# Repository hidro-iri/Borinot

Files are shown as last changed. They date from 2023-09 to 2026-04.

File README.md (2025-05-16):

# Borinot 🐝

<p align="center">
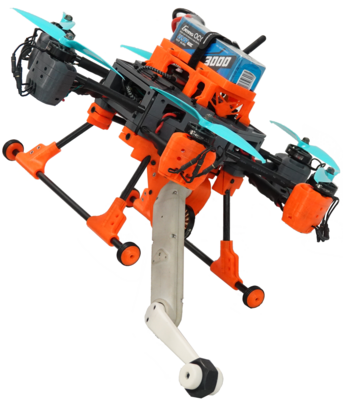
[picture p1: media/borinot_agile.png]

</p>

Borinot is an open-source, torque-controlled Unmanned Aerial Loco-Manipulator developed by the HiDRo group.  
It dynamically reconfigures its extremity as:
- A **tail** for agile flight  
- A **hand** for aerial manipulation  
- A **leg** for hybrid aerial-contact locomotion  

**Watch the demo**: [YouTube Presentation](https://www.youtube.com/watch?v=Ob7IIVB6P_A)

## Documentation  
Start by understanding the architecture and then assembling, configuring, and operating Borinot: 

| | |
| --- | --- |
| [**Borinot architecture**](architecture/README.md) | Understand the hardware and software architectures of Borinot |
| [**Hardware Assembly**](hardware/README.md) | Components list and instructions for assembling Borinot |
| [**Software Setup**](software/README.md) | Guide to Borinot's software stack installation, configuration, and subsystem integration |
| [**Operation Manual**](operation/README.md) | Instructions for operating Borinot and troubleshooting |

---

## Citation  
If Borinot contributes to your research, please cite:  

<!-- J. Martí-Saumell, H. Duarte, P. Grosch, J. Andrade-Cetto, A. Santamaria-Navarro, J. Solà. Borinot: an open thrust-torque-controlled robot for research on agile aerial-contact motion. arXiv preprint arXiv:2307.14686, 2023.-->

```bibtex
@misc{marti2023borinot,
  title={Borinot: An Open Thrust-Torque-Controlled Robot for Agile Aerial-Contact Motion Research},
  author={Martí-Saumell, Josep and Duarte, Hugo and Grosch, Patrick and Andrade-Cetto, Juan and Santamaria-Navarro, Angel and Solà, Joan},
  journal={arXiv preprint arXiv:2307.14686},
  year={2023}
}
```

## License
Borinot is licensed under the BSD 3-clause license. See [LICENSE](LICENSE) for details.

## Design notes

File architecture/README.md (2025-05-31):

# Borinot architecture

Borinot consists of hardware and software, both within the robot body and outside as necessary support elements.

This chapter describes the architecture. 

> You can click on the images below to get them in full resolution.

## Hardware

The Borinot robot consists of a flying platform and an arm, and is supported by some external equipments such as the Radio controller, the WIFI router, Optitrack and the base station or Laptop.

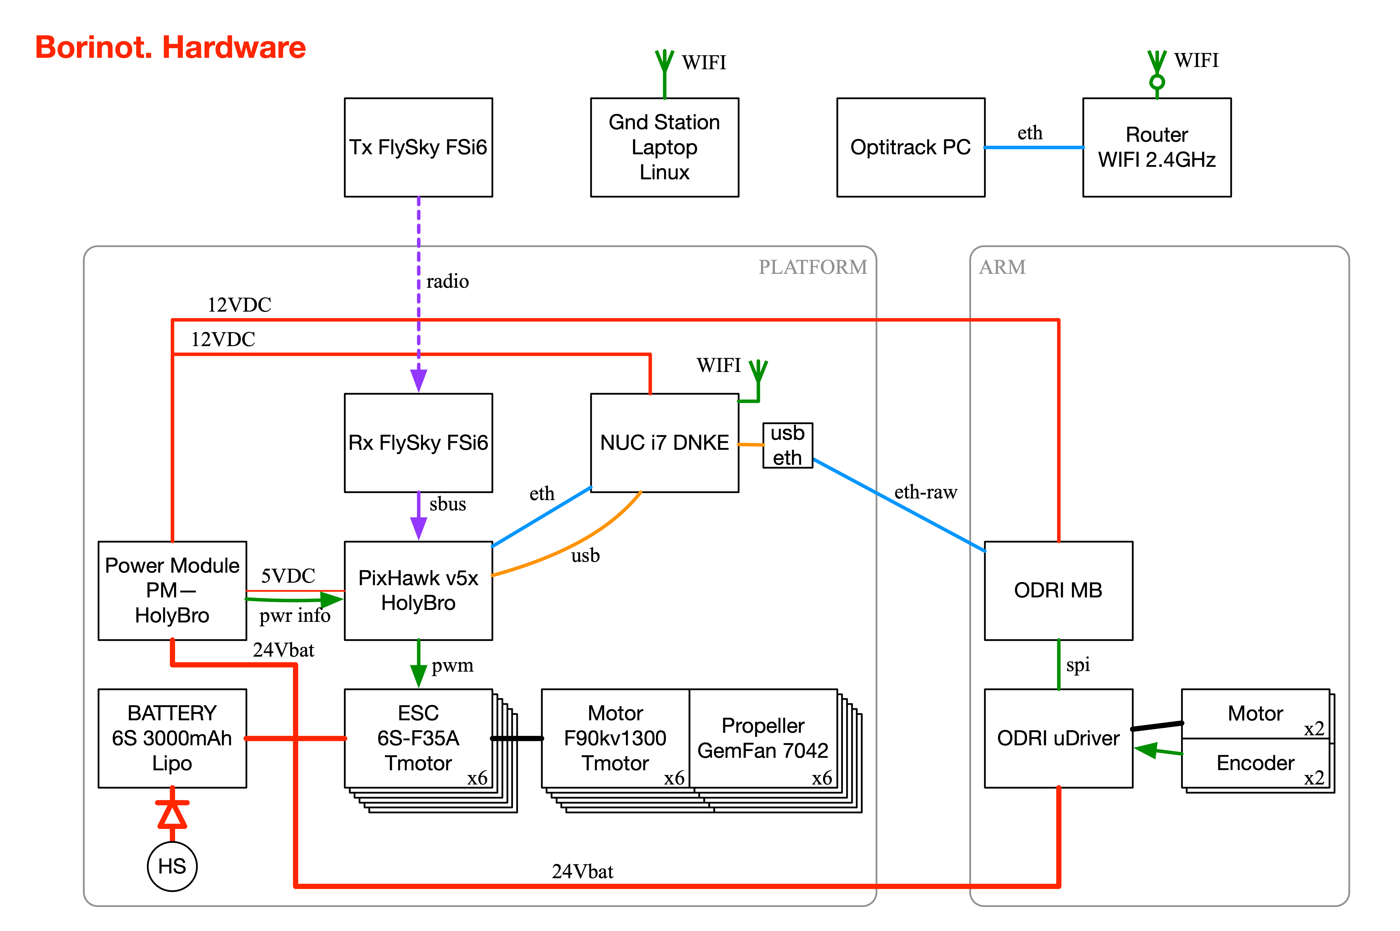
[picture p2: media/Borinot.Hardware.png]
Borinot Hardware


## Software

Borinot runs many pieces of software. Here, we detail the information flow for *estimation* (from sensors to computer) and *control* (from computer to motors). We also show the data flow for *simulations*.

### Software for state estimation

State estimation consists of fusing Borinot's IMU data with Optitrack position and orientation data.

The fusion is performed in the PixHawk unit by the EKF2 module.

The IMU data is gathered directly by PX4 in PixHawk

The Optitrack data is transferred from the Optitrack computer via wifi to Borinot's NUC, then via Ethernet to PX4 in Pixhawk.

The result of the estimation is send back to the NUC.

Additionally, the ODRI master board reports the arm state to the NUC via Ethernet.

The state `X` is located in the ROS2 node `StatePubSub`

Beware there are thre different reference frame conventions:
  - Optitrack uses `FUR`
  - PX4 uses `FRD`
  - ROS2 and Eagle MPC use `FLU`
  - The node `StatePubSub` in NUC transforms messages

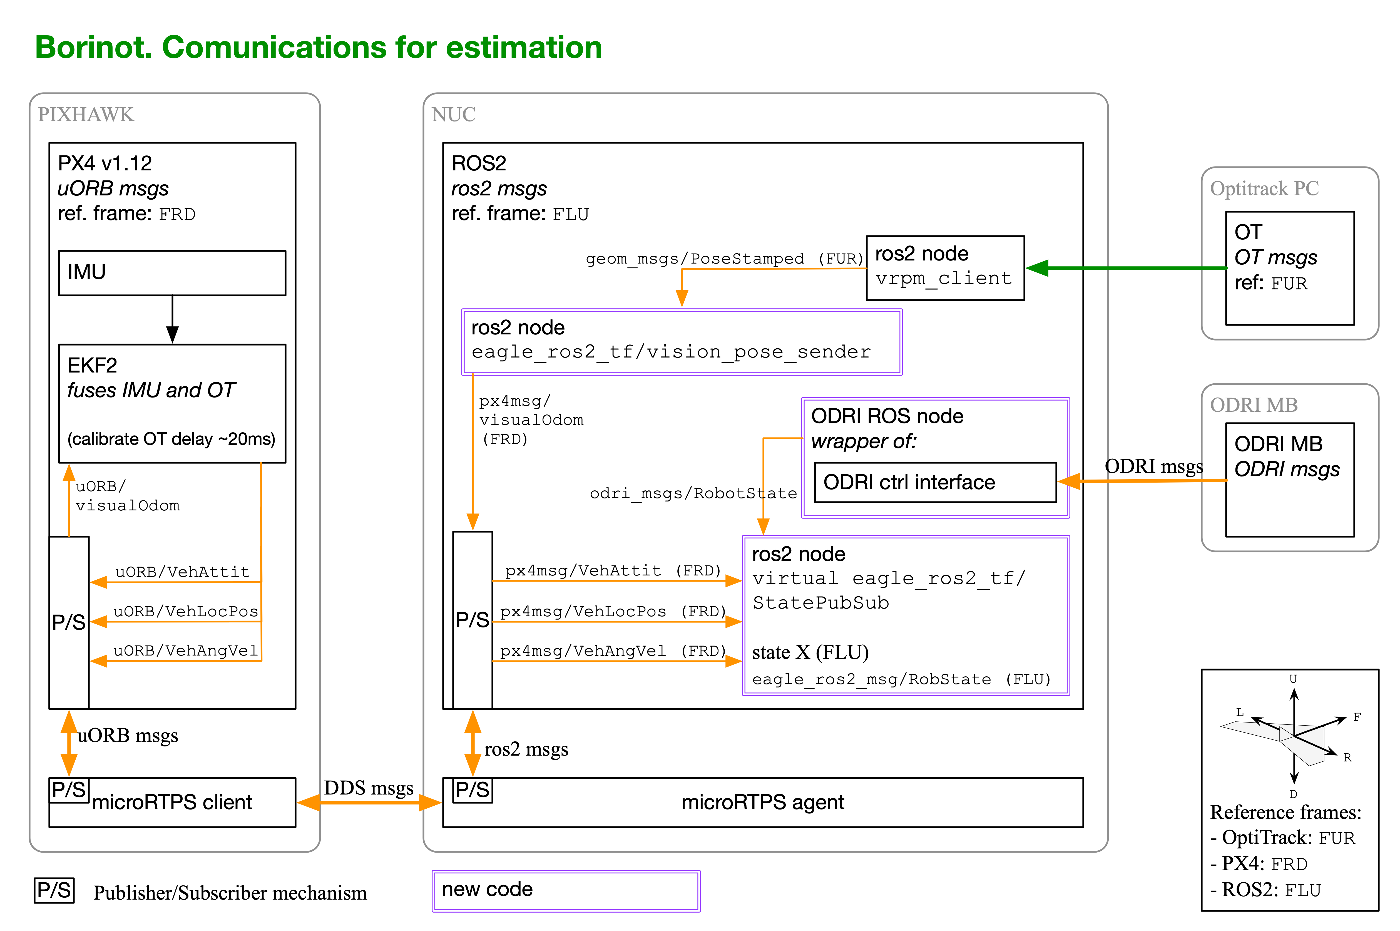
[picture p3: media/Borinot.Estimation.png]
Borinot Estimation


### Software for Control

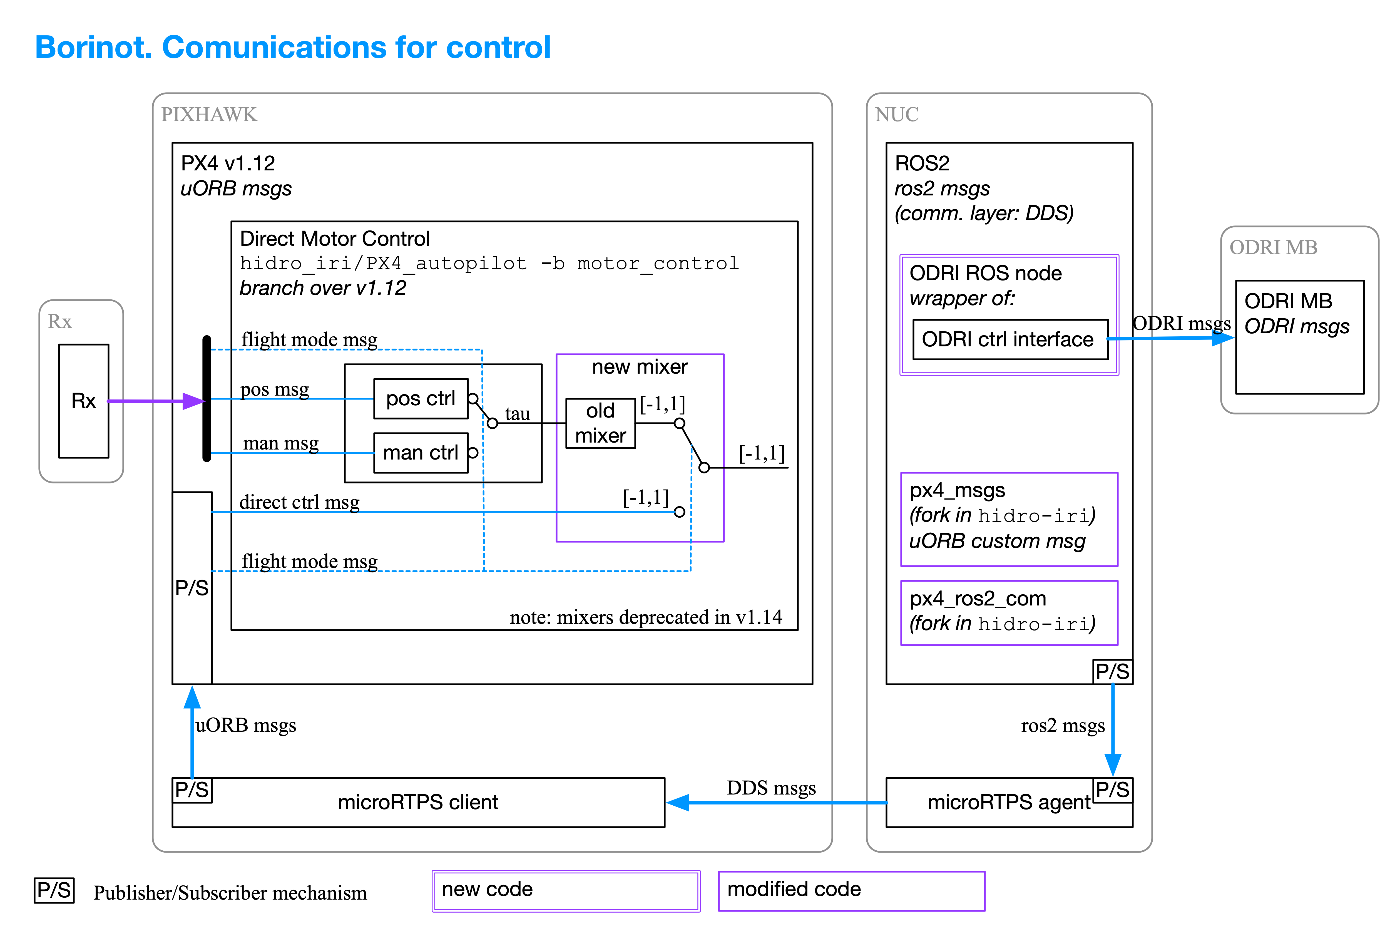
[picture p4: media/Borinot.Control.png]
Borinot Control


### Software for Simulation

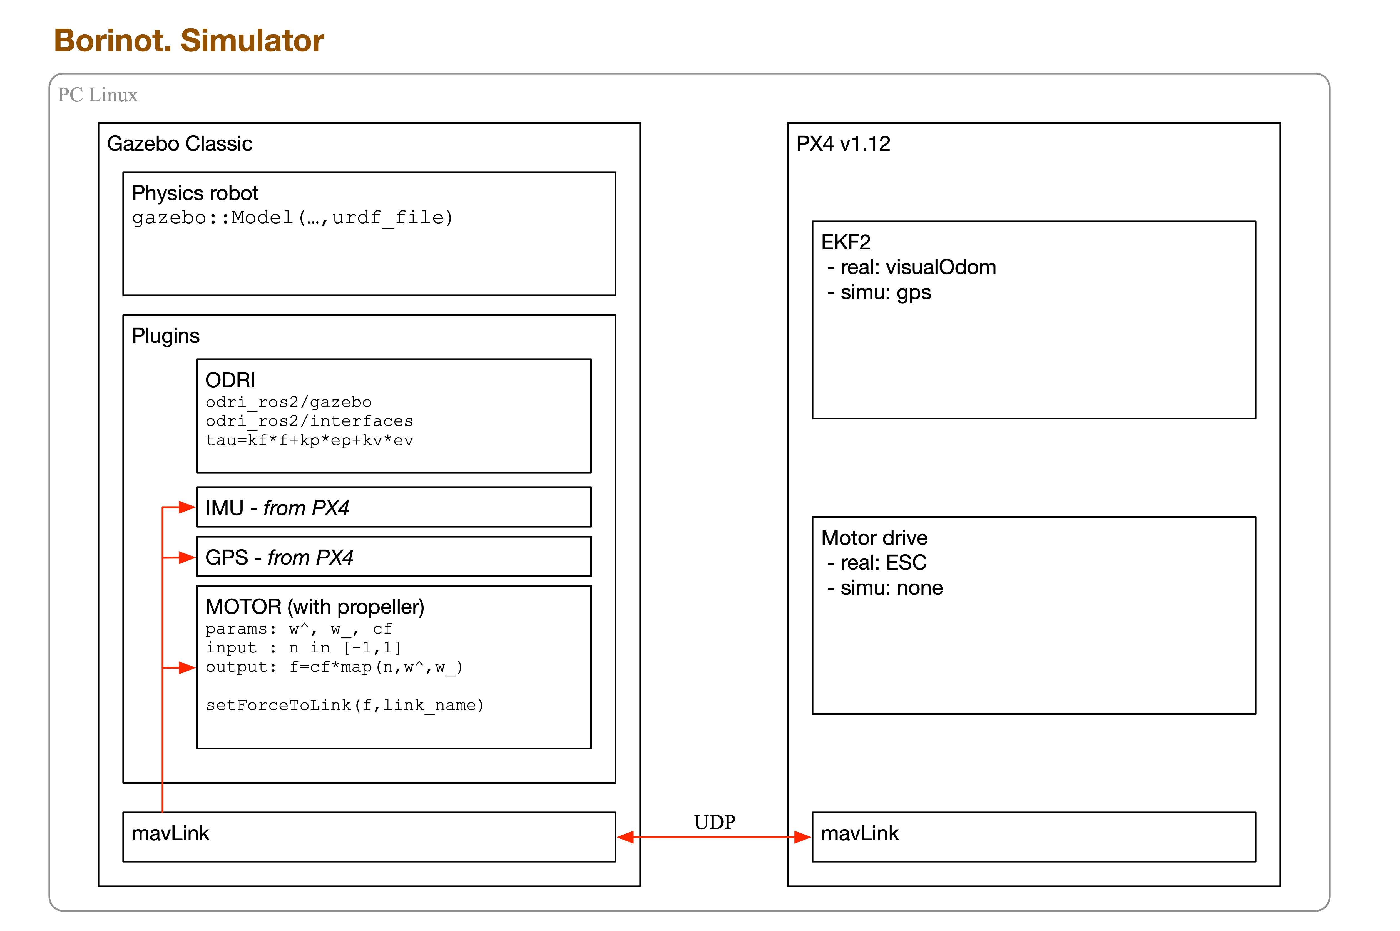
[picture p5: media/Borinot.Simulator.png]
Borinot Simulation


---

| [Top of page](#architecture) | [Back to Borinot HOME](../README.md) |
| --- | --- |

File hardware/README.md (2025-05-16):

# Borinot: Hardware Building Instructions

This guide provides a step-by-step overview of assembling Borinot. The assembly process is divided into two main sections: the **upper body** (steps 1 to 4) and the **lower body** (steps 5 to 7). Before you begin, ensure you have the necessary components (step 0).

**Contents:**

0. [**Components List**](0_components_list.md) - Full inventory of required parts.
1. [**Component Preparation**](1_component_preparation.md) - Modify power module and prepare motors/ESCs.
2. [**Airframe Assembly**](2_airframe_assembly.md) - Build motor cases and carbon fiber frame.
3. [**Main Body Assembly**](3_main_body_assembly.md) - Assemble core electronics in the main body case.
4. [**Upper Body Integration**](4_upper_body_integration.md) - Attach airframe to main body and route cables.
5. [**Landing Gear Assembly**](5_landing_gear_assembly.md) - Construct landing gear with dampers.
6. [**Flying Arm Assembly**](6_flying_arm_assembly.md) - Assemble ODRI actuator and controller case.
7. [**Lower Body Integration**](7_lower_body_integration.md) - Connect flying arm to landing gear and electronics.
8. [**Final Assembly**](8_final_assembly.md) - Combine upper and lower bodies.

---

| [Top of page](#borinot-hardware-building-instructions) | [Back to Borinot HOME](../README.md) |
| --- | --- |

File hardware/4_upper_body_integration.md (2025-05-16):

# Upper Body Integration

## 3D part 

### Materials

- 3d parts (spacers)
- nuts M3 (x8)

### Steps

1. clean plastic
2. put nuts

## Airframe Mounting

### Materials

- Main Body
- Airframe
- 3D parts

### steps

1. Place the main body on top of the airframe keeping the fronts align.
> :information_source: each CF tube should fit inside the CFT slots.  
> ⚠️  if one triangle does not fit, place properly two tubes and reassemble the two others motor cases to make the third bare fits.  
2. Put the medium spacer between the differents carbon fiber tubes and tight them with fasterner.
> ⚠️  The slots should be facing out.  
> :information_source: The spacer is place at the intersections of the carbon fibers tube. (seeing from the top)  
> :information_source: use the main body's inside cavity to hide the head of the fasteners.
> ⚠️  be careful to not fastern cables in it.
> :Cut the oer part of the fasterner. 

3. Put all the other spacers where they should go.
> ⚠️  The slots should be facing out.  
> :information_source: The spacer is place at the intersections of the carbon fibers tube. (seeing from the top)  
> :information_source: The more distance between two tubes, the bigger the spacers

4. For each landing gear interface, put it in place and tight it using fasterner.
> ⚠️  The slots should be facing out.  
> :info_source: The interface should fit just below the spacer.
> :information_source: use the main body's inside cavity to hide the head of the fasteners.
> ⚠️  be careful to not fastern cables in it.
> :Cut the oer part of the fasterner. 

- 2. Put one spacer between the differents carbon fiber tubes (start with the medium ones, then the big ones, then the small one).

- smaller between top and middle
- medium between middle and bottom
- large between top and bottom

- 3. if the spacer if touching the lower bares (small and big ones), put the associate landing gear interface below the spacer

- 4. Tight the airframe to the main body where the spacer is using fasteners

- 5. repeat steps 2 to 4 for each spacer.

## Upper Body Routing

> ⚠️  Patience is key.

### Materials

- USB-C cable
- receiver cable
- spiral attach

### steps

> Put a top view of the frame with the bar colored with the type of cable that should be passing through.

Motors connected to the Power module back : 1, 4, 6
Motors connected to the Power module front : 2, 3, 5

- signal cable goes to the bare that put them close to the back of the Pixhawk

1. Follow the routing schematic. (picture showing on which should pass each cable.)
    > Signal and Power cables should be twisted properly to ensure 
2. Continue with the signal cables.
3. Start by the power cables
4. Connect the signal cable following the [Hexarotor X airframe reference](https://docs.px4.io/main/en/airframes/airframe_reference.html#hexarotor-x). 
    > :information_source: To identify the proper cable (i.e cable number i) between all, proceed as follow: maintain the signal cable i on the motor side (as you are sure it is the good one), on the pixhawk side, pull each cable one by one, if you feel some force on the motor side, you have the good one!

4. Finish with the other cables.
    - From Pixhawk : ethernet !!! , power (should be already connected at main body assembly), serial bus (usb-c) [also to pixhawk] !!!,
    - From the computer : ethernet extender !!!, wifi antenna,
    - From power module : microcontroller cable, masterboard cable,
    - From radio receiver : two antennas,  radio receiver, 

5. Put the spiral to maintain the cable with the frame.
    - cable should pass below the tube
    - `Assure that the cables are properly twisted!!!`
    - Radio antenna should be put above the tube

6. 
---

| [Top of page](#upper-body-integration) | [Back to Hardware Building Instructions](README.md) | [Back to Borinot HOME](../README.md) | [Next → Landing Gear Assembly](5_landing_gear_assembly.md) |
| --- | --- | --- | --- |

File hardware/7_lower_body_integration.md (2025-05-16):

# Borinot: Lower Body Assembly Guide

The lower body is an important part of borinot. It's contains the arm and the associated low level controller and the landing gear. This part can be assembled to Borinot to give him access to an arm.

## Components List

| Part Name | Quantity | Description | Reference |
|---|:---:|---|---|
| [Controller Case - 3D Kit](CAD/platform/) | 1 | - | [Link to the part](CAD/platform/) |
| Master Board | 1 | - | - |
| Micro Driver | 1 | - | - |
| M2 Nuts | 4 | - | - |
| M2.5 Nuts | 4 | - | - |
| M2x6mm Screws | 4 | - | - |
| M2.5x6mm Screws | 4 | - | - |

## Assembly Guide

### Prerequisite: Landing Gear and Flying Arm

The [Landing Gear](landing_gear.md) and the [Flying Arm](flying_arm.md) have they own guide to simplifly the assembly. Please go refer to them if these parts are not yet assembled.

### Part 1: Controller Case

The controller case contains all the electronics require to control the arm. It contains a microcontroller have is connected to the motors and encoders of the arm. It also contain the masterboard, interface between the computer and the microcontroller. Both of these board are powered using the Power module contains in the Upper Body. In order to assemble it properly, we have to first clean the 3D printing and put the nuts and other mechanical components together. After that the boards have to be connected together and finally we can assemble everything.

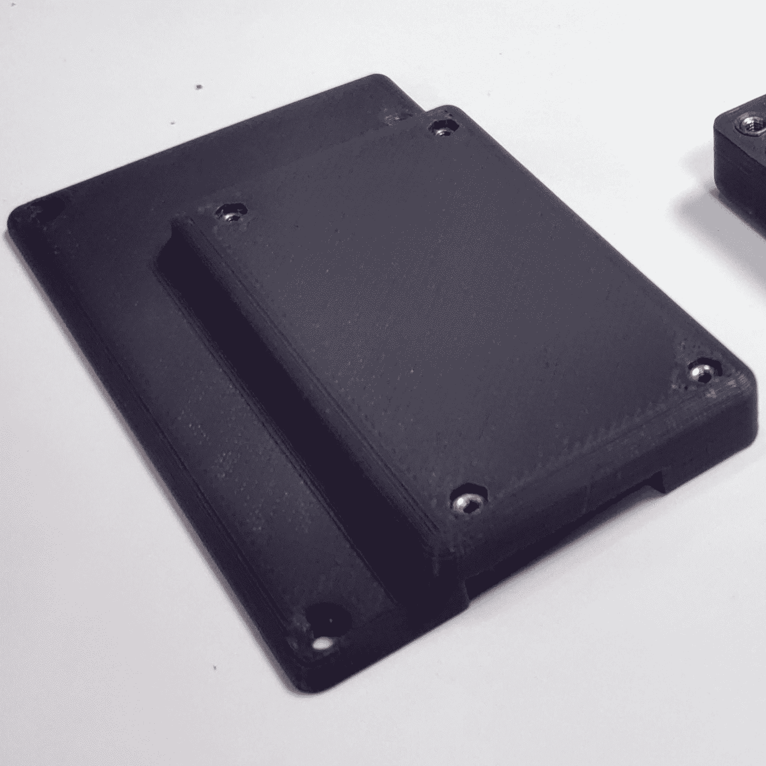
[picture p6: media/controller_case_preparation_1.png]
Top view of the motor case 3 assembly

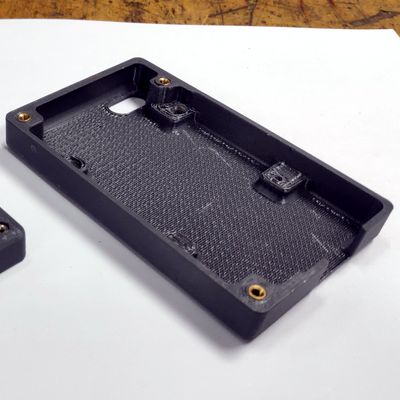
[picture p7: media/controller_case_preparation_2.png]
Top view of the motor case 3 assembly


- **Clean all parts of the Controller Case - 3D Kit**.
- **Insert M2 Nuts, M2.5 Nuts, and M3 Inserts in their designated slots in the 3D kit components**.
- **Connect the two links to the micro driver. Ensure the cable routes through the designated holes in both the controller and flying cases**.

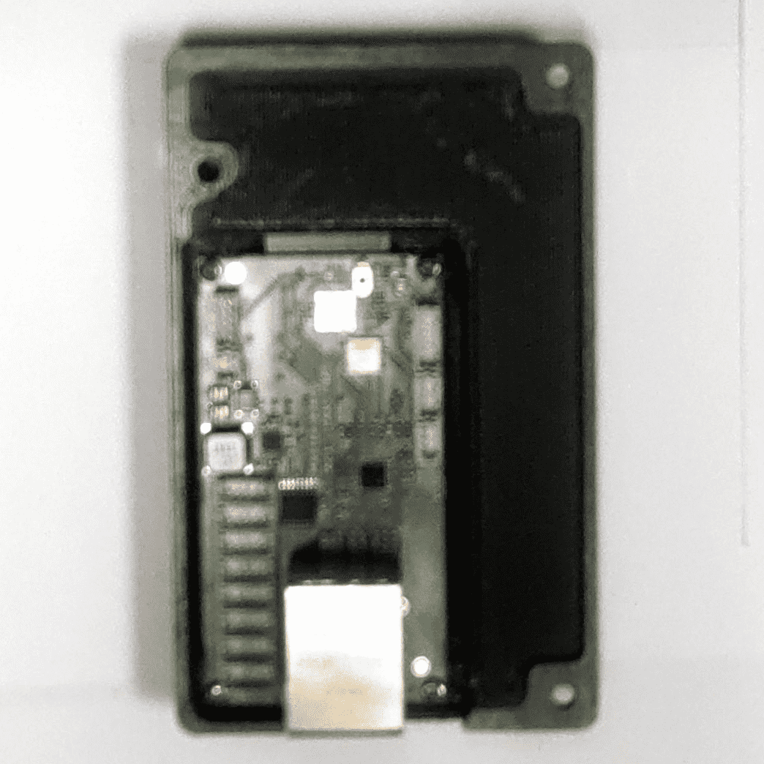
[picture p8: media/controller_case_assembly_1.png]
Top view of the motor case 3 assembly

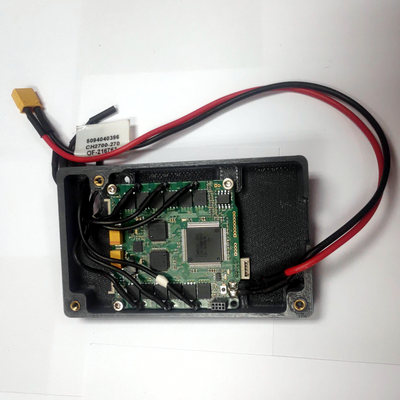
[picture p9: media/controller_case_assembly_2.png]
Top view of the motor case 3 assembly


- **Establish a connection between the micro driver and the master board.**
- **Secure the master board inside the controller case - top using M2 screws**.
- **Mount the micro driver at the bottom of the controller case, securing with M2.5 screws**.
- **Close the case using 3 M3 screws**.

### Part 2: Assembly

The controller case and the arm are holded by the landing gear. The last step is to attach the arm to the landing gear.

- **Using 6 M3 screws, attach the arm to the landing gear.**

---

| [Top of page](#borinot-lower-body-assembly-guide) | [Back to Hardware Building Instructions](README.md) | [Back to Borinot HOME](../README.md) | [Next → Final Assembly](8_final_assembly.md) |
| --- | --- | --- | --- |

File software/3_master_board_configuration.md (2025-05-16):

# Master Board Configuration

> ⚠️  Since some libraries are no longer actively maintained, version conflicts may occur in the future. If something doesn't work during the installation process, it could be due to a dependency that needs to be downgraded. ⚠️ 

Part 1: Master Board SDK Installation
1. **Build** and **install** forked Master Board SDK from source:
> :information_source: The original Master Board SDK repository has been forked to converse an older version compatible with the rest of the system.  
> The modified version is avalaible [here](https://github.com/hidro-iri/master-board).
``` bash
cd ~/libraries
git clone --recursive https://github.com/hidro-iri/master-board.git -b flying_arm
cd master-board/sdk/master_board_sdk
mkdir build && cd build
cmake -DCMAKE_BUILD_TYPE=Release ..
make -j6
sudo make install
```
2. Use `ip address` to get the name of the interface
> :information_source: there is normally two ethernet interfaces. `eno1` is used by the Pixhawk. The master board uses the **`OTHER ONE`**.
> :information_source: Note somewhere the name of the used interface (`MY_INTERFACE`) as it will be required for thew second part.

3. Run the example inside build folder:
``` bash
cd ~/libraries/master-board/sdk/master_board_sdk/build
sudo ./master_board_example MY_INTERFACE
```
where `MY_INTERFACE` is the name of the ethernet interface used to connect to the master board.

Part 2: Odri Control Interface Installation
1. **Build** and **install** forked Odri Control Interface from source:
> :information_source: The original Odri Control Interface repository has been forked to converse an older version compatible with the rest of the system.  
> The modified version is avalaible [here](https://github.com/hidro-iri/odri_control_interface).
``` bash
cd ~/libraries
git clone --recursive https://github.com/hidro-iri/odri_control_interface.git -b flying_arm
cd odri_control_interface
mkdir build && cd build
cmake -DCMAKE_BUILD_TYPE=Release ..
make -j6
sudo make install
```
2. Test the example
```

sudo ./
```

---
| [Top of page](#master-board-configuration) | [Back to Software Setup Guide](README.md) | [Back to Borinot HOME](../README.md) | [Next → ROS2 Installation & Configuration](4_ros2_workspace.md) |
| --- | --- | --- | --- |

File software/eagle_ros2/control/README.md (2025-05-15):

# Eagle ROS2: Control

This package contains different nodes that allow to interact with the UAM. There are some basic nodes that can be used to test more advanced control architectures.

## 1. Basic (abstract) nodes
The Eagle MPC-ROS2 control package has several abstract (or base) classes. These, are common pieces used on a wide variety of control architectures for real robots.
1. We need to get the state estimation of the robot.
2. We need to compute a control (using some fancy algorithm) and send it to the actuators
3. It is good to have a state machine that ensures the good operation of the robot: a proper initialization of data structures and algorithms, a proper ending of algorithms, acceptable handling of unexpected situations, to provide a user interface, etc.

This package contains these pieces implemented as abstract classes. The idea is to build our final control architecture inheriting from the ones that we need. In the following, there is a small explanation of each one of them.

### 1.1 State subscriber & publisher
This node subscribes to different topics containing the state of the robot and publishes the state in one single message. All the callback sbelong to a `callback_group` to ease the running of this node (and its eventual derived ones) on a `MultithreadExecutor`.

Even being a base class, it can still be run as a stand-alone node. The steps to get this node running in simulation are the following:

> :information_source: To gain insight into the detailed launching procedure [go here](../../../procedures/preflight.md). This procedure is automatized by means of ROS2 launch files.

1. Start the PX4 simulation:
```console
foo@bar:~/$ cd <path-to-px4-autopilot>
foo@bar:<path-to-px4-autopilot>/$ make px4_sitl_rtps gazebo
```
2. In a second terminal, source your ROS2 workspace and run the following command:
```console
foo@bar:<path-to-ros2-ws>/$ ros2 launch eagle_ros2_control state_pub_sub.launch.py
```
3. In a third, confirm that the state is being published as a single message:
```console
foo@bar:<path-to-ros2-ws>/$ ros2 topic echo /platform_state
```

### 1.2 Base controller

This provides the basic functionality to write commands to the UAM actuators (thrust and torque). It is built as a pure virtual class. As such, it must be derived in a separate class so that it can be used.

It has only one pure virtual function called `computeControls()`, which is where the derived classes will call the control algorithms to get the controls for the robot. This is called in its own callback group and, therefore, it is easy to assign an own thread when doing the final node executor. This function is called at fixed rate, specified by a parameter.

Since it is a pure virtual class, it cannot be launched as a standalone application.

### 1.3 State machine

Generally, to have an operating robot, we need to go through different launch procedures. In these, we make sure that every single subsystem is properly initialized. To ease these procedure we have implemented an abstract class containing a state machine.

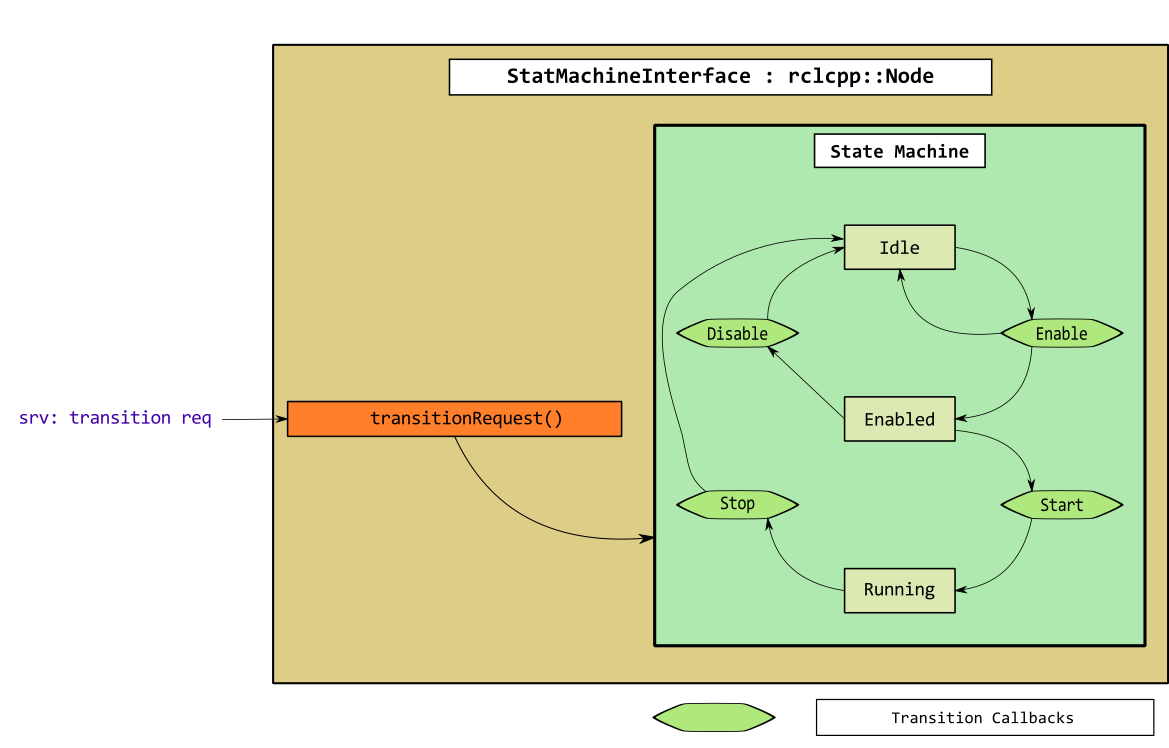
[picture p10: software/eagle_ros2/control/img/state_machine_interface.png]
Node structure


**FINISH EXPLANATION!**

## 2. Utility (derived) nodes
### 2.1 Control Manager Interface
This is a node with a more advanced functionality. Contains the machinery to run the control based on MPC.

[See here](ctrl_mgr_interface.md) for more info.

### 2.2 Decentralized controller
This is a node to control separately the flying platform and the robotic arm of a UAM.

[See here](decentralized_controller.md) for more info.

[Back to Eagle MPC - ROS2](../README.md)

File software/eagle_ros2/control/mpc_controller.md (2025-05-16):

# Eagle MPC ROS2: Control -> MPC Controller
This node incorporates functionalities to interact with the UAM by using the `eagle_mpc::ControlManager` object. This object is in charge of ensuring a continuous operation of the UAM using MPC controllers (see diagram below).

What the node **DOES NOT** do:
- To manage the MPC controllers or any other algorithmic issue related to the MPC algorithm. This is left for the class [`eagle_mpc::ControlManager`](https://github.com/hidro-iri/eagle_mpc_lib/blob/devel/include/eagle_mpc/controller-manager.hpp).

What the node **DOES**:
- To address the robot's state data coming both from PX4 and the ODRI master board.
- To address the actuator's commands computed by the `eagle_mpc::ControlManager` to the corresponding actuator topics/drivers.
- To manage a state machine to safely operate the UAM.

You can skip the implementation details and go directly to the [practical details](#2-operation) about how to operate a UAM with this node.

## 1 Architecture

Let us explain its functionality with the help of the diagram below:

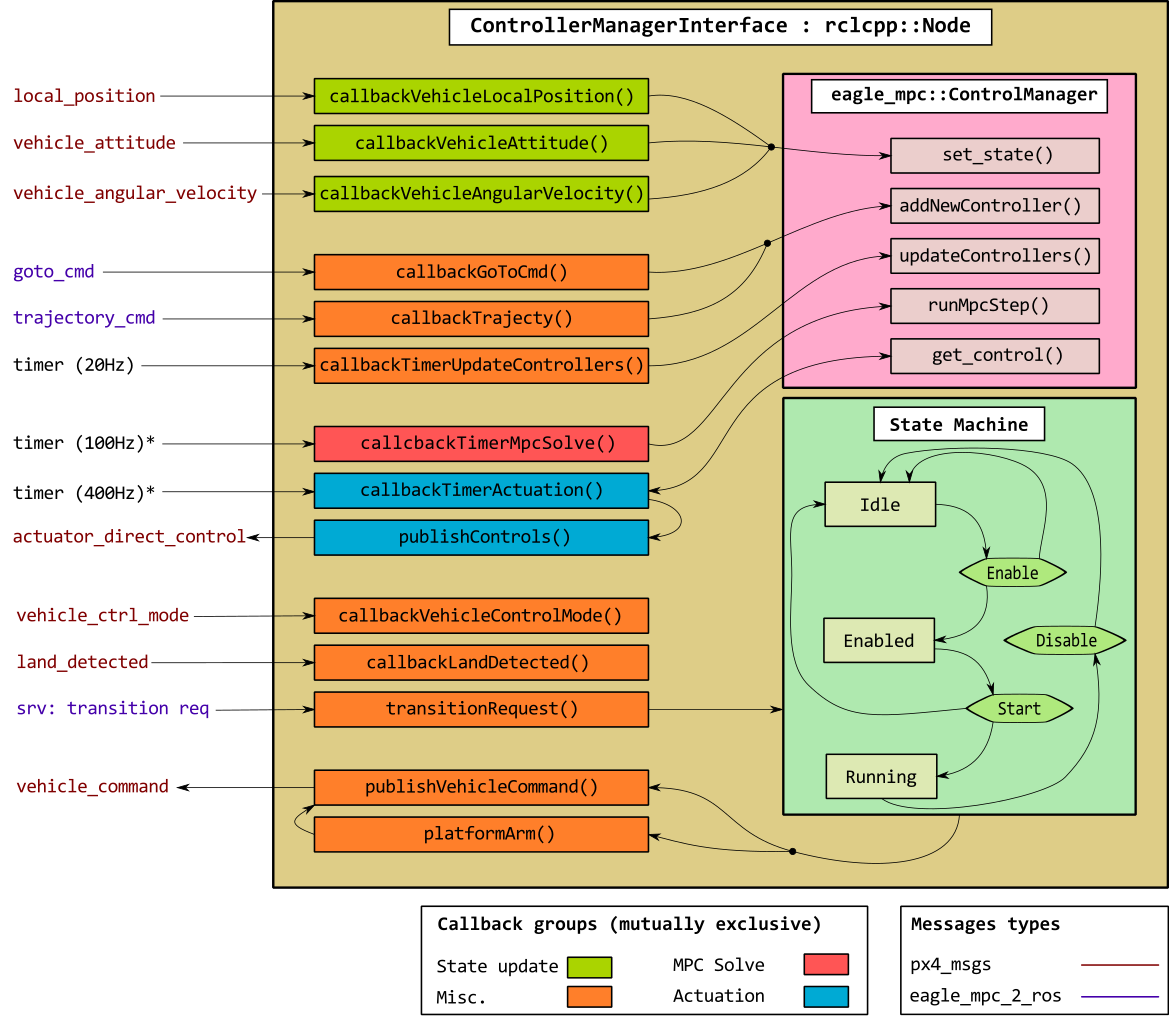
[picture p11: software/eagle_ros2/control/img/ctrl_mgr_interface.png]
Node structure


### 1.1 State machine

The node is governed by a state machine with three main states:

- **Idle**: The base is `disarmed` if the UAM is `landed`. Flight mode is the PX4-standard `pos_ctl`. Nothing is being published to `vehicle_command` topic.
- **Enabled**: The base is `armed` and the UAM `landed`. Flight mode is the custom `direct-control` mode. Zeros are being published to the `vehicle_command` topic waiting for the first MPC solution to be computed.
- **Running**: The base is armed and the UAM `flying`. Flight mode is the custom `direct-control` mode. The MPC controls are being published to the `vehicle_command` topic.

There is a ROS2 service to ask for a transition to occur. When this service is called, the callback `transitionRequest` is executed. If the right conditions are met, the state transitions from the current state to the requested one. 

- **Idle** &#8594; **Enabled**:
  - State machine must be **Idle**
  - The `MicroRTPS Agent` must be running and publishing to the state topics.
  - Vehicle must be landed.
- **Enabled** &#8594; **Running**: this transition is done automatically once the PX4 landed flag is set to false. Conditions checking happens inside `callbackLandDetected()`.
  - State machine must be **Enabled**
  - Vehicle must be landed
  - Not landed flag received in the callback message.
  - Motor Control flight mode must be enabled.
- **Running** &#8594; **Idle**:
  - State machine must be **Running**

### 1.2 Callbacks
The node spins in a multithreaded executor. Each callback is assigned to a `callback_group`, which is mutually exclusive. That is, for a specific `callback_group`, one and only one callback from this group can be executed simultaneously. In our case, as we have four groups, at maximum there will be four callbacks executing simultaneously.

These are the `callback_groups`:
- **State update** (callbacks in green), *time-critical*: 
  - Callbacks of subscribers for topics carrying robot's state information (e.g. position, attitude, joint configuration, ...).
  - Always updating state in the `ControlManager` object.
- **Controls update** (callback in blue), *time-critical*: 
  - the only callback in this group is responsible for getting the control from the `eagle_mpc::ControlManager` and publish it oto the  `actuator_direct_control` topic.
- **MPC solve** (callback in red), *time-critical*: 
  - the only callback in this group is responsible for calling. `eagle_mpc::ControlManager::runMpcStep()`.
- **Miscellaneous** (callback in orange) *time-non-critical*:
  - callbacks related to the PX4 status.
  - callbacks interacting with the state machine (e.g. change the flight mode).
  - callback to update the status of the `eagle_mpc::ControlManager` object.
  - callbacks for the topics carrying mission commands, i.e., `callbackGoToCmd` and `callbackTrajectoryCmd`

## 2 Operation

### 2.1 Build with the appropriate messages
To run this node you should first have compiled the `PX4-Autopilot` and the `px4_ros_com` by using the messges in `px4_control_msgs.yaml` and `ros2_control_msgs.yaml`, respectively.

[Build procedure](../README.md#2-build)

### 2.2 Launch the required systems

1. Start the PX4 simulation:
```console
foo@bar:~/$ cd <path-to-px4-autopilot>
foo@bar:<path-to-px4-autopilot>/$ make px4_sitl_rtps gazebo
```
2. In a second terminal, source your ROS2 workspace and run the following command:
```console
foo@bar:<path-to-ros2-ws>/$ ros2 launch eagle_ros2_control mpc_controller.launch.py
```
3. In a third termimal, publish a GoTo command:
```console
foo@bar:~$ ros2 topic pub -1 /goto_command eagle_mpc_2_interfaces/msg/GoToCmd "{platform_pos:{x: 0, y: 0, z: 2}, platform_yaw: 90, time: 2500}"
```
4. Now, you can enable the MpcController:
```console
foo@bar:~$ ros2 service call /mpc_controller/state_transition eagle_mpc_2_interfaces/srv/TransitionCommand "{command: enable}"
```

---

| [Top of page](#eagle-mpc-ros2-control---mpc-controller) | [Back to Eagle MPC - ROS2 Control](README.md) | [Back to Software](../README.md) |
| --- | --- | --- |

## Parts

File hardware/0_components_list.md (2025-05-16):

# Components List

Before beginning assembly, ensure you have all necessary components on hand. This list is organized into categories for ease of reference.

## Upper Part

<!-- Put Picture of all the piece of the upper part -->
<!-- Plus comment of the picture -->

| Part Name | Quantity | Description | Reference |
|---|---|---|---|
| PM03D Power Module | 1 | Base unit | [Holybro](https://holybro.com/products/pm03d-power-module) |
| EC5-M Connector | 1 | Male battery connector | [TME](https://www.tme.eu/es/en/details/ec5-m/dc-power-connectors/amass/) |
| XT30-F Connector | 1 | Female power connector | [RC Innovations](https://rc-innovations.es/shop/amass-conector-xt30-hembra-xt30u-h) |
| XT30-M Connector | 1 | Male power connector | [RC Innovations](https://rc-innovations.es/shop/amass-conector-xt30-macho-xt30u-m) |
| Diode | 1 | | `BQ30TB 45B714` |
| Red Power Cable | 2 | 15cm 16AWG (VCC) | [RC Innovations](https://rc-innovations.es/shop/Cable-silicona-16AWG-Rojo-1-metro-amass) |
| Black Power Cable | 2 | 15cm 16AWG (GND) | [RC Innovations](https://rc-innovations.es/shop/cable-de-silicona-26-awg-negro-1-metro) |
| Computer Cable | 1 | 24cm barrel plug (5.5×2.5mm) | [Amazon](https://www.amazon.com/Generic-5-5mm-2-5mm-Right-Pigtail/dp/B07H38LNPD) |
| Masterboard Cable | 1 | 17cm line | |
| Connector JST | 1 | Male | |

| Part Name | Quantity | Type | Assembly Reference |
|:-|:-:|:-:|:-|
| [Motor Cases](CAD/motor_case/) | 6 | 3D part | [Airframe Assembly](building_instructions.md#airframe-assembly) |
| [Body Case](CAD/body_case/) | 1 | 3D part | [Body Assembly](building_instructions.md#body-assembly) |
| [Landing Gear](CAD/landing_gear/) | 1 | | [Landing Gear Assembly](building_instructions.md#landing-gear-assembly) |
| [Controller Case](CAD/controller_case/) | 1 | | [Controller Assembly](building_instructions.md#controller-assembly) |
| [2DOF Flying Arm](CAD/flying_arm/) | 1 | | [Flying Arm Assembly](building_instructions.md#flying-arm-assembly) |
| [TMotor F90-1300KV](https://store.tmotor.com/goods.php?id=1064) | 6 | | [Airframe Assembly](building_instructions.md#airframe-assembly) |
| [TMotor F35A 6s](https://store.tmotor.com/goods.php?id=1176) | 6 | | [Airframe Assembly](building_instructions.md#airframe-assembly) |
| [NUC i7](https://ark.intel.com/content/www/us/en/ark/products/series/217835/intel-nuc-kit-with-12th-generation-intel-core-processors.html) | 1 | | [Body Assembly](building_instructions.md#body-assembly) |
| [PixHawk5](https://docs.px4.io/main/en/flight_controller/pixhawk5x.html) | 1 | | [Body Assembly](building_instructions.md#body-assembly) |
| ø**...**mm O-ring Seals | 24 | | [Airframe Assembly](building_instructions.md#airframe-assembly) | <!--Mechanical Components-->
| ø20mm O-ring Seals | 12 | | [Landing Gear Assembly](building_instructions.md#landing-gear-assembly) |
| M3x5mm Screws | 12 | | [Airframe Assembly](building_instructions.md#airframe-assembly) |
| M3x10mm Screws | 8 | | [Landing Gear Assembly](building_instructions.md#landing-gear-assembly) |
| M3x10mm Nylon Screws | 6 | | [Airframe Assembly](building_instructions.md#airframe-assembly) |
| M3x16mm Screws | 8 | | [Landing Gear Assembly](building_instructions.md#landing-gear-assembly) |
| M3x30mm Screws | 24 | | [Airframe Assembly](building_instructions.md#airframe-assembly) |
| M4 Nuts | 6 | | [Airframe Assembly](building_instructions.md#airframe-assembly) |
| M3 Nuts | 16 | | [Landing Gear Assembly](building_instructions.md#landing-gear-assembly) |
| M3 Inserts | 12 | | [Airframe Assembly](building_instructions.md#airframe-assembly) |
| Cable Ties | 6 | | [Body Assembly](building_instructions.md#body-assembly) |
| ø8mmx110.0mm Carbon Fiber Round Tubes | 4 | | [Landing Gear Assembly](building_instructions.md#landing-gear-assembly) |
| ø8mmx170.0mm Carbon Fiber Round Tubes | 2 | | [Landing Gear Assembly](building_instructions.md#landing-gear-assembly) |
| ø8mmx300.0mm Carbon Fiber Round Tubes | 2 | | [Landing Gear Assembly](building_instructions.md#landing-gear-assembly) |
| ø8mmx352.5mm Carbon Fiber Round Tubes | 6 | | [Airframe Assembly](building_instructions.md#airframe-assembly) |
| [Markers](https://optitrack.com/accessories/markers/#mcm-14.0-m4-10) | 11 | | [Airframe Assembly](building_instructions.md#airframe-assembly) & [Body Assembly](building_instructions.md#body-assembly)|

## Lower Part

## Electronics

- **Computer:** Intel [NUC i7](https://ark.intel.com/content/www/us/en/ark/products/series/217835/intel-nuc-kit-with-12th-generation-intel-core-processors.html)
- **Flight Controller:** [PixHawk5](https://docs.px4.io/main/en/flight_controller/pixhawk5x.html)
- **Power Module:** [PM03D Power Module](https://holybro.com/collections/power-modules-pdbs/products/pm03d-power-module)
- **ESC:** [TMotor F35A 6s](https://store.tmotor.com/goods.php?id=1176)
- **Control Board:** [Master board](https://github.com/open-dynamic-robot-initiative/master-board#master-board) from [ODRI](https://github.com/open-dynamic-robot-initiative)
- **Driver:** [Micro Driver](https://github.com/open-dynamic-robot-initiative/open_robot_actuator_hardware/tree/master/electronics/micro_driver_electronics) from ODRI
- **Actuator:** [Actuator Module](https://github.com/open-dynamic-robot-initiative/open_robot_actuator_hardware/blob/master/mechanics/actuator_module_v1/README.md) from ODRI

## 3D Printed Parts

- **Motor Case:** Comprising a *top*, two *middles*, a *bottom*, and a *cache*.
- **Body Case:** Consisting of a *top*, a *crown*, a *bottom*, and two sizes of *tube holders (S,M, and L)*.
- **Landing Gear:** Including four *attachments*, four *feet*, and four *pawns*.
- **Controller Case:** Consisting of a *top* and a *bottom*.
- **2DOF Flying Arm**

## Bill of Materials - Borinot

| Part Name | Quantity | Comments | Assembly Reference |
|:-|:-:|:-:|:-|
| [Motor Cases](CAD/motor_case/) | 6 | | [Airframe Assembly](building_instructions.md#airframe-assembly) |
| [Body Case](CAD/body_case/) | 1 | | [Body Assembly](building_instructions.md#body-assembly) |
| [Landing Gear](CAD/landing_gear/) | 1 | | [Landing Gear Assembly](building_instructions.md#landing-gear-assembly) |
| [Controller Case](CAD/controller_case/) | 1 | | [Controller Assembly](building_instructions.md#controller-assembly) |
| [2DOF Flying Arm](CAD/flying_arm/) | 1 | | [Flying Arm Assembly](building_instructions.md#flying-arm-assembly) |
| [TMotor F90-1300KV](https://store.tmotor.com/goods.php?id=1064) | 6 | | [Airframe Assembly](building_instructions.md#airframe-assembly) |
| [TMotor F35A 6s](https://store.tmotor.com/goods.php?id=1176) | 6 | | [Airframe Assembly](building_instructions.md#airframe-assembly) |
| [NUC i7](https://ark.intel.com/content/www/us/en/ark/products/series/217835/intel-nuc-kit-with-12th-generation-intel-core-processors.html) | 1 | | [Body Assembly](building_instructions.md#body-assembly) |
| [PixHawk5](https://docs.px4.io/main/en/flight_controller/pixhawk5x.html) | 1 | | [Body Assembly](building_instructions.md#body-assembly) |
| ø**...**mm O-ring Seals | 24 | | [Airframe Assembly](building_instructions.md#airframe-assembly) | <!--Mechanical Components-->
| ø20mm O-ring Seals | 12 | | [Landing Gear Assembly](building_instructions.md#landing-gear-assembly) |
| M3x5mm Screws | 12 | | [Airframe Assembly](building_instructions.md#airframe-assembly) |
| M3x10mm Screws | 8 | | [Landing Gear Assembly](building_instructions.md#landing-gear-assembly) |
| M3x10mm Nylon Screws | 6 | | [Airframe Assembly](building_instructions.md#airframe-assembly) |
| M3x16mm Screws | 8 | | [Landing Gear Assembly](building_instructions.md#landing-gear-assembly) |
| M3x30mm Screws | 24 | | [Airframe Assembly](building_instructions.md#airframe-assembly) |
| M4 Nuts | 6 | | [Airframe Assembly](building_instructions.md#airframe-assembly) |
| M3 Nuts | 16 | | [Landing Gear Assembly](building_instructions.md#landing-gear-assembly) |
| M3 Inserts | 12 | | [Airframe Assembly](building_instructions.md#airframe-assembly) |
| Cable Ties | 6 | | [Body Assembly](building_instructions.md#body-assembly) |
| ø8mmx110.0mm Carbon Fiber Round Tubes | 4 | | [Landing Gear Assembly](building_instructions.md#landing-gear-assembly) |
| ø8mmx170.0mm Carbon Fiber Round Tubes | 2 | | [Landing Gear Assembly](building_instructions.md#landing-gear-assembly) |
| ø8mmx300.0mm Carbon Fiber Round Tubes | 2 | | [Landing Gear Assembly](building_instructions.md#landing-gear-assembly) |
| ø8mmx352.5mm Carbon Fiber Round Tubes | 6 | | [Airframe Assembly](building_instructions.md#airframe-assembly) |
| [Markers](https://optitrack.com/accessories/markers/#mcm-14.0-m4-10) | 11 | | [Airframe Assembly](building_instructions.md#airframe-assembly) & [Body Assembly](building_instructions.md#body-assembly)|

---
| [Top of page](#components-list) | [Back to Hardware Building Instructions](README.md) | [Back to Borinot HOME](../README.md) | [Next → Component Preparation](1_component_preparation.md) |
| --- | --- | --- | --- |

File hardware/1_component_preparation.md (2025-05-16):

# Component Preparation Guide

Some components require modifications before assembling. This guide covers adjustments needed for the power module, brushless motors, and ESCs.

---

## Part 1: Power Module Modification

The Power Module distributes power to all components (computer, motors, arm, flight controller) and monitors battery status via Pixhawk.

### Materials

materials for power module modification

> **Top view list**
> - computer cable (`#8`)
> - power module (`#1`)
> - masterboard power cable (`#9`) with JST connectors (`#10`)
> - EC5 connector (`#2`)
> - XT30-F connector (`#3`)
> - diode (`#5`)
> - XT30-M connector (`#4`)
> - red (`#6`) and black (`#7`) power cables

| ID | Part Name | Qty | Description | Location | Reference |
|---|---|-----|---|---|---|
| `#1`  | PM03D Power Module | 1 | Base unit | HS- | Holybro |
| `#2`  | EC5-M Connector | 1 | Male battery connector | HS- | TME |
| `#3`  | XT30-F Connector | 1 | Female power connector | HS- | RC Innovations |
| `#4`  | XT30-M Connector | 1 | Male power connector | HS- | RC Innovations |
| `#5`  | Diode | 1 | BQ30TB 45B714 | HS- | - |
| `#6`  | Red Power Cable | 2 | 15cm 16AWG Silicon | HS- | RC Innovations |
| `#7`  | Black Power Cable | 2 | 15cm 16AWG Silicon | HS- | RC Innovations |
| `#8`  | Computer Cable | 1 | 24cm barrel plug (5.5×2.5mm) | HS- | Amazon |
| `#9`  | Masterboard Cable | 1 | 17cm line | HS- | ODRI |
| `#10` | Connector JST | 1 | Male | HS- | RC Innovations |

### Steps

Step 1A: Unsoldering original XT60 connector from PM03D (Component #1) 
Step 1B: EC5-M connector installed on power module (Component #2)

> **Battery Cable Modification**  
> Left: Original XT60 configuration | Right: Modified EC5 connector installation

1. **Unsolder** the capacitor and battery cable from the board (`#1`).
2. **Replace** the battery cable's connector from XT60 to EC5 (`#2`).
   
   > ⚠️  Do not cut the cable to remove the XT60.  
   > :information_source: Apply pressure when inserting EC5 terminals into housing.

3. **Resolder** the capacitor and battery cable so they point **inward** on the board.

---

Step 4-7: Hot-swap cable assembly - Diode (#5) and XT30-M (#4) before heat shrink 
Step 4-7: Hot-swap cable completed - Heat shrink applied to XT30-M (#4) connections

> **Hot-Swap Cable Assembly**  
> Left: Pre-sealed assembly showing diode (#5) and XT30-M (#4) connections | Right: Finished cable with insulated joints

4. **Bend** the diode's (`#5`) anode (right leg) to connect with the positive terminal of the XT30-M connector (`#4`) and **solder**.
5. **Solder** the diode's cathode (left leg) to the positive power cable (`#6`).
6. **Solder** the negative power cable (`#7`) to the negative terminal of the XT30-M connector.
7. **Add** heat shrink tubing over the connectors and **heat** to seal.  
   > :information_source: This becomes the **hot-swap cable** - compare your result with right image above.
8. **Solder** the hot-swap cable to the battery cable location, keeping the same orientation (**See final picture of the part**).

---

Step 9-10: Microdriver cable components - XT30-M (#4), red (#6) & black (#7) cables unsoldered 
Step 9-10: Completed microdriver cable - XT30-M (#4) with heat shrunk connections

> **Microdriver Cable Assembly**  
> Left: Preparation stage | Right: Finished assembly  
> Components: XT30-F connector (`#5`), red 16AWG (`#6`), black 16AWG (`#7`)

9. **Solder** both power cables to XT30-F connector (`#5`):
   - Red (`#6`) → Positive terminal
   - Black (`#7`) → Negative terminal

10. **Add** heat shrink tubing and **seal** connections.  
    > :information_source: Now referred to as **microdriver cable** - compare with right image.
11. **Solder** microdriver cable to board:
   - Red (`#6`) → B+ pad
   - Black (`#7`) → GND pad  
   > ⚠️  Apply heat shrink over connector before use (as shown right).
---

Masterboard components

> **Top view: Components for masterboard cable (from right to left: masterboard power cable, JST male connector, JST female connector)**

12. **Cut** the masterboard power cable in half.
13. **Crimp** JST connector onto each cable.
    > ⚠️  Be sure to put the connector the correct way to ensure positive-to-positive alignment.

14. **Use** the connector-bearing cable for the [flying arm assembly](6_flying_arm_assembly.md) and the other as the **masterboard cable**.
15. **Solder** the masterboard cable to the **5V com pin**, ensuring proper polarity (black cable to ground, green cable to 5V).
    > :information_source: Add heat shrink over exposed pins for safety.

---

Computer components

> **Close view: VDD jumper pins (middle left) and computer cable at servo pin (lower right)**

16. **Set VDD to 12V** using the jumper configuration.
17. **Cut** the computer cable to a **24cm length**.
18. **Solder** the computer cable to the **VDD servo pin**, maintaining correct polarity.
    > :information_source: Cover solder joints with heat shrink tubing.

---

Modified power module

> **Top view: Final modified power module**

---

## Part 2: Brushless Motor and ESC Modification

In this part you’ll modify both the brushless motors and the ESCs. Follow the steps closely to ensure proper electrical connections and maintain correct polarity.

### Materials

Exploded view of brushless motor components

> **Top view: Components for motor and ESC modification (from top to bottom, left to right: servo connector, ESC, motor, servo pins, power cables, banana plug, XT30-M connector, signal cables)**

| Part Name | Quantity | Description | Reference |
|---|:---:|---|---|
| TMotor F90-1300KV | 6 | Brushless motor | [TMotor](https://store.tmotor.com/goods.php?id=1064) |
| Banana Plug (male) | 18 | 3.5 mm, male | [RC Innovations](https://rc-innovations.es/shop/con00000438-conector-banana-3-5mm-tipo-tmotor-pareja-18644)  |
| TMotor F35A 6s | 6 | ESC | [TMotor](https://store.tmotor.com/goods.php?id=1176) |
| Red Power Cable | 6 | 30cm Silicone 16 AWG cable in Red | [RC Innovations](https://rc-innovations.es/shop/Cable-silicona-16AWG-Rojo-1-metro-amass) |
| Black Power Cable | 6 | 30cm Silicone 16 AWG cable in Black | [RC Innovations](https://rc-innovations.es/shop/Cable-silicona-16AWG-Negro-1-metro-amass) |
| White Servo Cable | 6 | 30cm Silicone 26 AWG cable in White | [RC Innovations](https://rc-innovations.es/shop/Cable-de-silicona-26AWG-blanco-1-metro) |
| Black Servo Cable | 6 | 30cm Silicone 26 AWG cable in Black | [RC Innovations](https://rc-innovations.es/shop/cable-de-silicona-26-awg-negro-1-metro) |
| Banana Plug (female)  | 18 | 3.5 mm, female | [RC Innovations](https://rc-innovations.es/shop/con00000438-conector-banana-3-5mm-tipo-tmotor-pareja-18644)  |
| XT30 Connector (male) | 6 | XT30 male connector | [RC Innovations](https://rc-innovations.es/shop/amass-conector-xt30-macho-xt30u-m) |
| Servo Connector | 6 | Female | [RC Innovations](https://rc-innovations.es/shop/Conector-servo-Futaba-hembra) |

### Steps

#### Brushless Motor Modification

Brushless motor modification

> **Top view: Motor and banana plugs (from left to right)**

1. **Trim** the phase cables by about **5cm**.  
   > ⚠️  Retain the trimmed segments for the ESC modification.
2. **Solder** the male banana plugs to the trimmed phase cables.  
   > :information_source: Use the connector’s side hole to help evenly melt the solder paste.
3. **Add** heat shrink tubing around the connectors to insulate the soldered joints.
4. **Repeat** these steps for all 6 brushless motors.

---

Modified brushless motor

> **Close view: Finalized motor**

#### ESC Modification

ESC modification

> **Close view: ESC faces – Left/Middle ones show pads labeled `–`, `S`, and `T` for signal cables at the bottom left. Right one shows power cable pads at the top; displays phase cable pads at the bottom**

5. **Solder** 5cm of the leftover phase cables from the motors to the ESC’s phase pads.
6. **Attach** the female banana plugs to these phase cables and **add** heat shrink tubing over the connections before heating to seal.
7. **Solder** 30cm power cables to the ESC’s power pads.  
   > :information_source: Connect the red cable to the positive (`+`) pad and the black cable to the negative (`–`) pad.
8. **Slide** heat shrink tubing onto both power cables (do not heat yet).
9. **Solder** the XT30 male connectors to the ends of the power cables.  
   > ⚠️  Double-check polarity before sealing.
10. **Heat** the tubing to secure the connections.

---

ESC servo connector orientation

11. **Solder** 30cm servo cables to the ESC’s servo pads.  
    > :information_source: Attach the white cable to the signal (S) pad and the black cable to the ground (–) pad.
12. **Crimp** the wires and attach the servo connectors.  
    > ⚠️  Orientation matters - white wire must align with signal (S) pad position.  
    > Match connector notch with ESC's plastic alignment tab.

13. **Repeat** the entire ESC modification process for all 6 ESCs.

---

Modified ESC

> **Top view: Finalized modified ESC**

---
| [Top of page](#component-preparation-guide) | [Back to Hardware Building Instructions](README.md) | [Back to Borinot HOME](../README.md) | [Next → Airframe Assembly](2_airframe_assembly.md) |
| --- | --- | --- | --- |

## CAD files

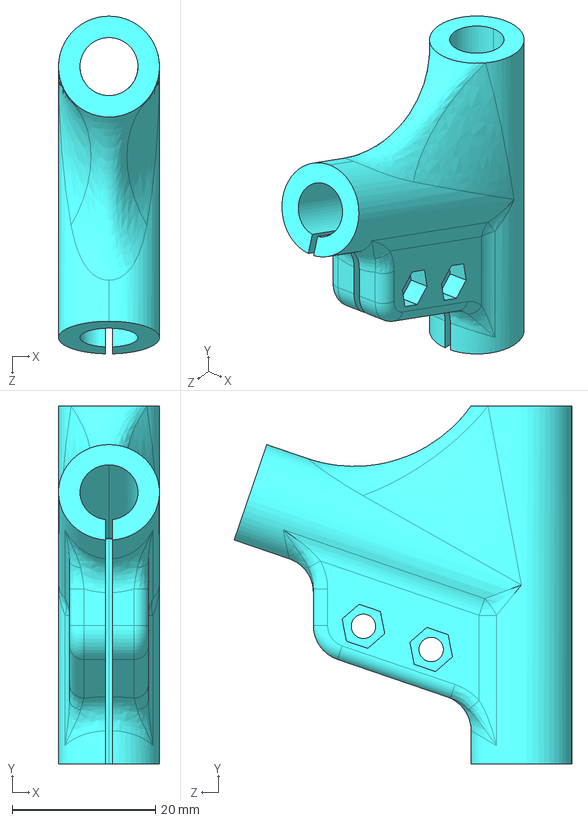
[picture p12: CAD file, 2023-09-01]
hardware/cad_files/legs/rod_connector_wye.STEP
14.1 x 50.0 x 47.2 mm

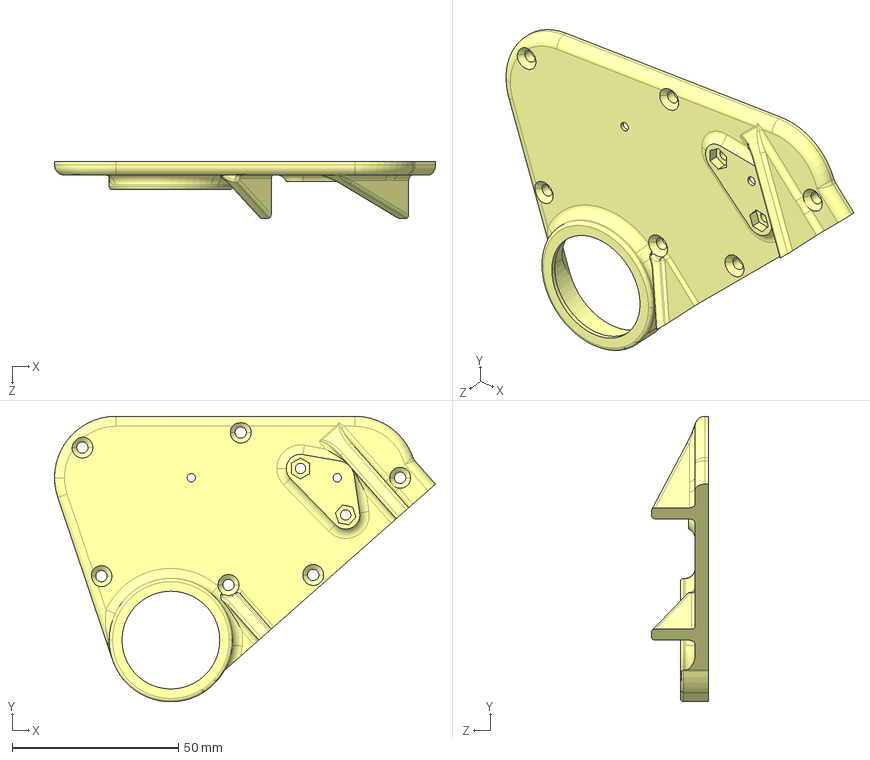
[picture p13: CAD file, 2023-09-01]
hardware/cad_files/limb/case_flying_link_b.STEP
114.6 x 85.8 x 17.0 mm

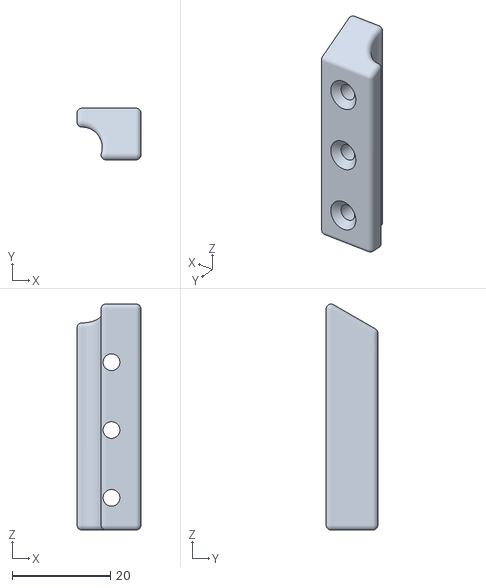
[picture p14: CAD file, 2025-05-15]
hardware/cad_files/lower_body/flying_arm_press_right.stl
13.0 x 10.5 x 46.0

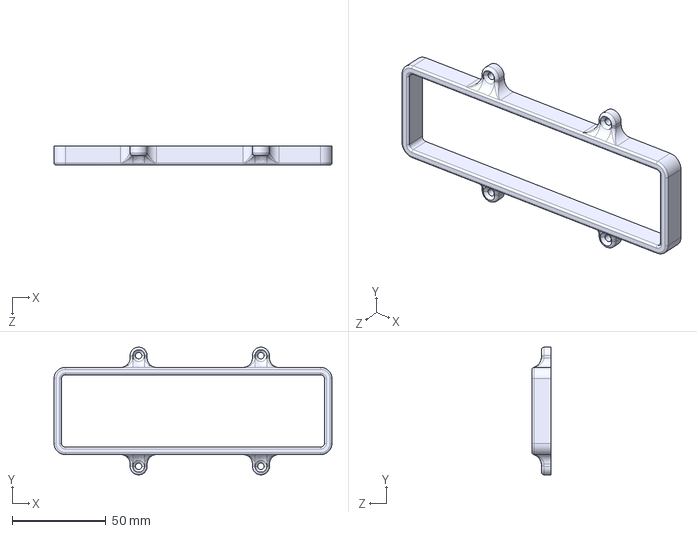
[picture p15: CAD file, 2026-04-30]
hardware/cad_files/main_body/Battery_holder.STEP
148.0 x 68.0 x 10.0 mm

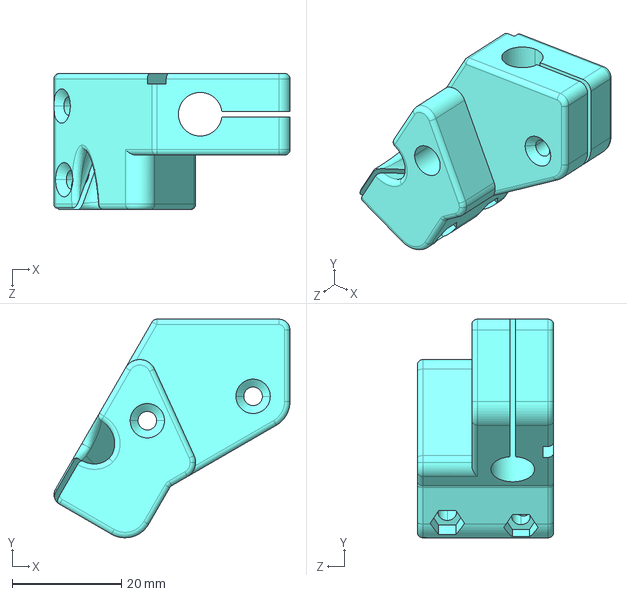
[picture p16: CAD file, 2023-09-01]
hardware/cad_files/legs/rod_connector_cross_block_a.STEP
43.3 x 40.1 x 25.0 mm

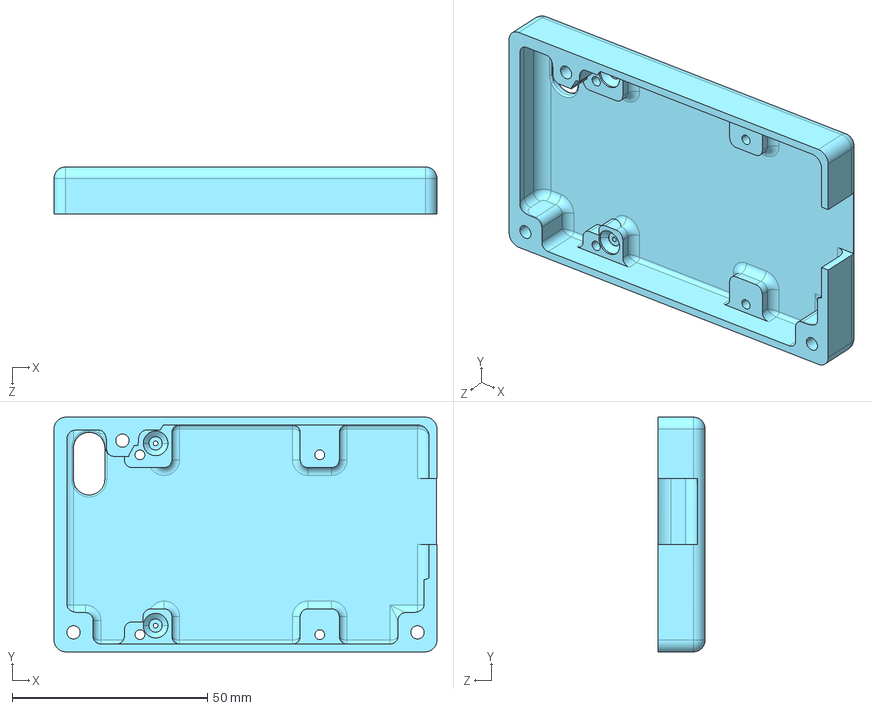
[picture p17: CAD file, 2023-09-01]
hardware/cad_files/limb/case_controller_bottom.STEP
98.0 x 60.1 x 12.1 mm

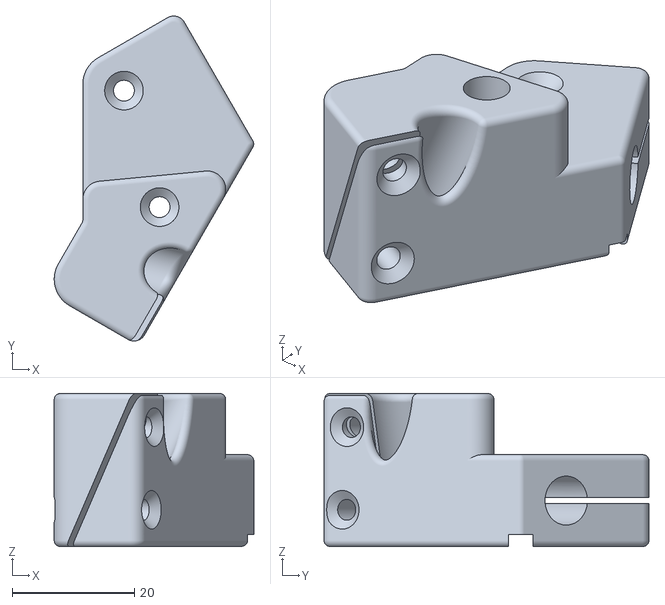
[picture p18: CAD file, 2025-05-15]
hardware/cad_files/lower_body/landing_gear_union_upper_b.stl
32.6 x 53.1 x 25.0

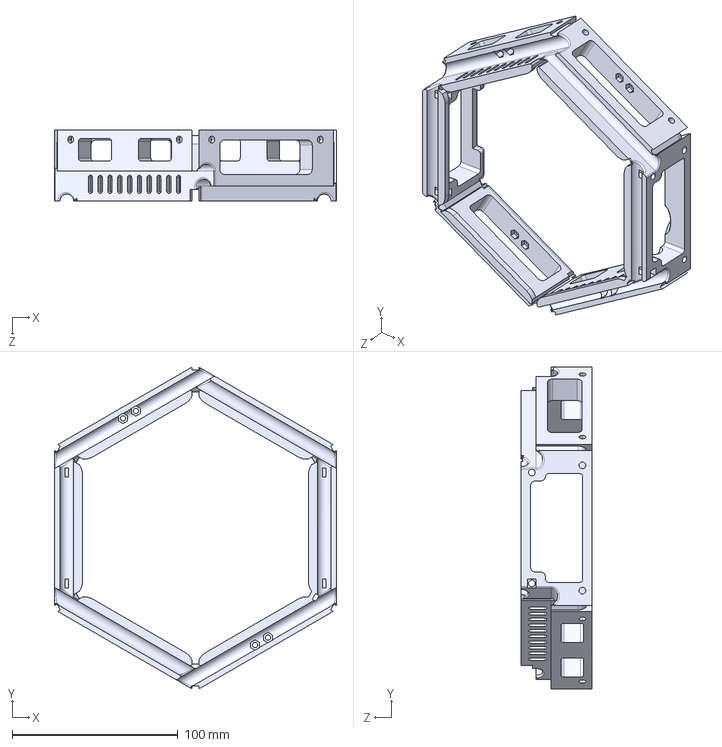
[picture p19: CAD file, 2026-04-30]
hardware/cad_files/main_body/hex_stack_a.STEP
170.4 x 194.5 x 42.7 mm

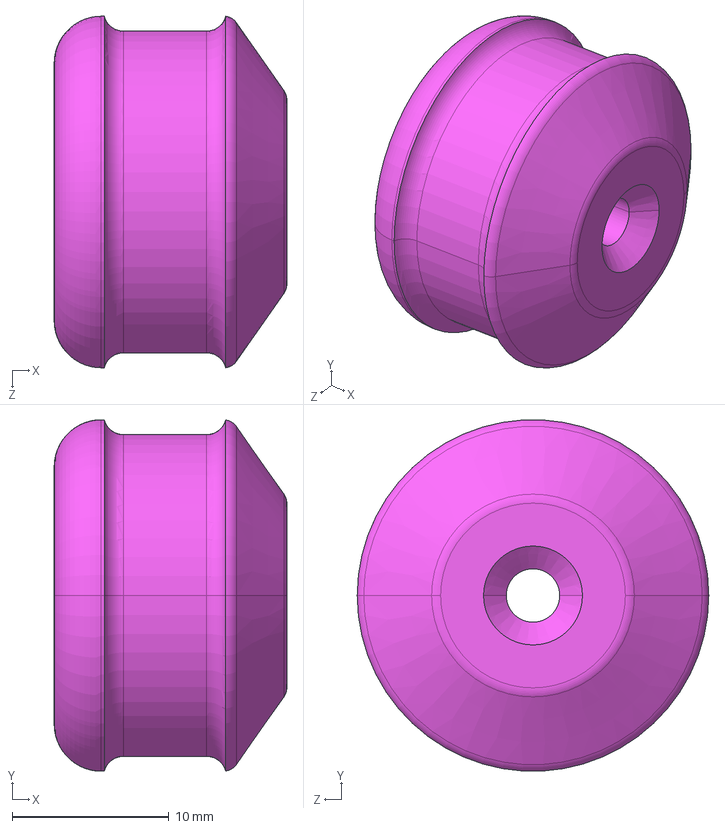
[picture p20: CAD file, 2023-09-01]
hardware/cad_files/legs/rod_cap_shock_absorber.STEP
14.8 x 22.4 x 22.4 mm

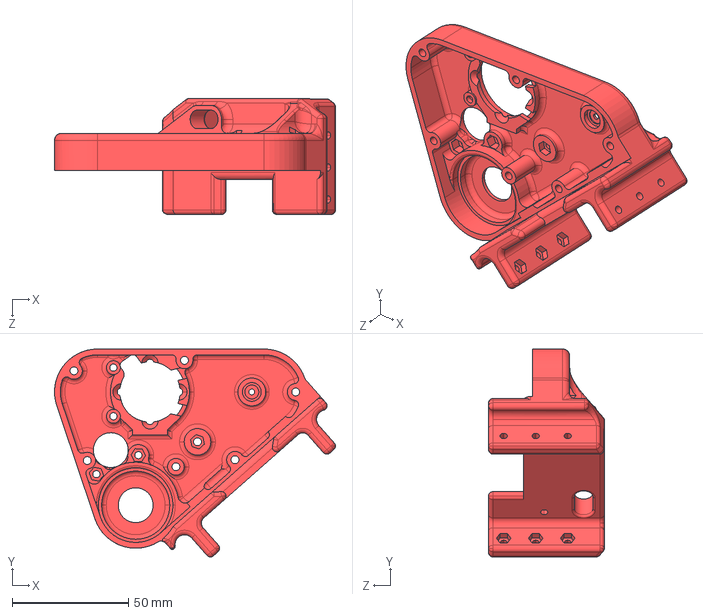
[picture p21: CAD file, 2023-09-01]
hardware/cad_files/limb/case_flying_link_a.STEP
121.1 x 89.6 x 50.0 mm

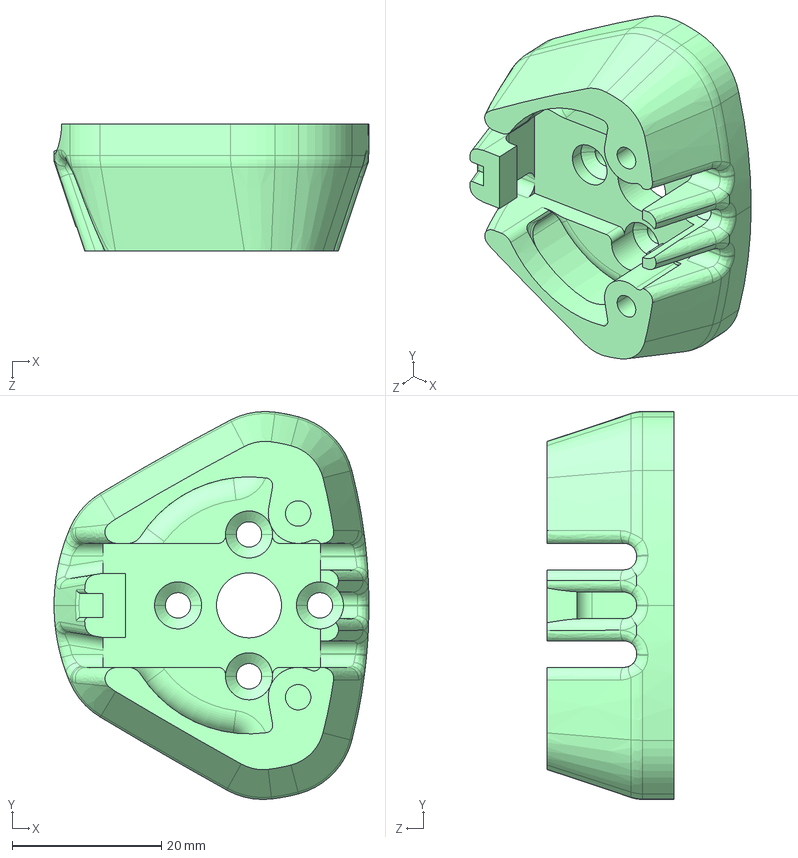
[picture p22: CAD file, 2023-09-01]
hardware/cad_files/main_body/motor_holder_d.STEP
42.2 x 52.0 x 17.0 mm

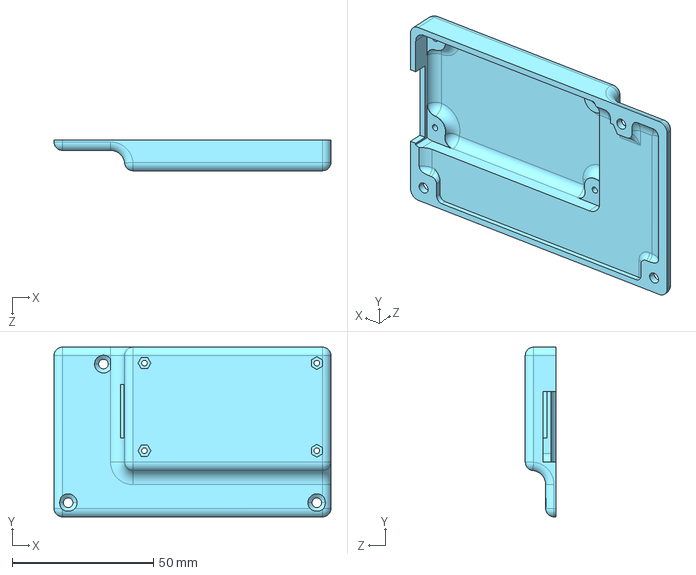
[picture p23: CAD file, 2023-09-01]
hardware/cad_files/limb/case_controller_top.STEP
98.0 x 60.1 x 10.8 mm

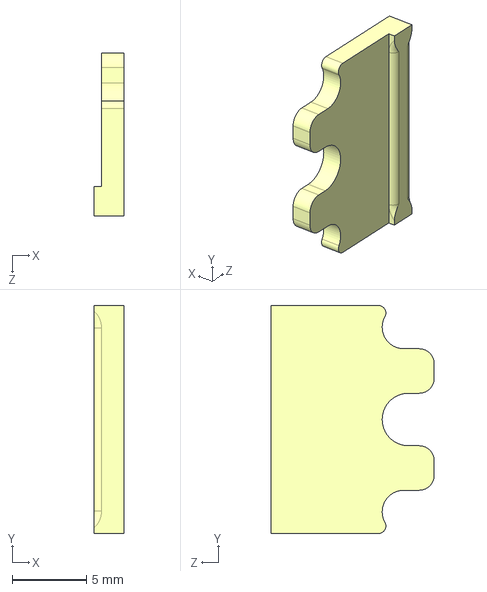
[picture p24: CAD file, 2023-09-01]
hardware/cad_files/main_body/motor_holder_g.STEP
2.00 x 15.4 x 11.0 mm

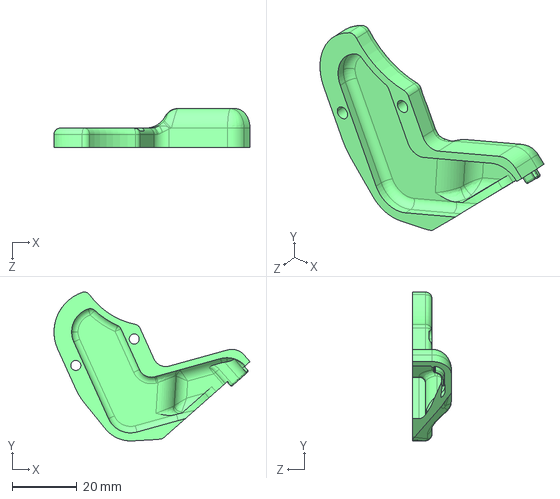
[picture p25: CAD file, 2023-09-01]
hardware/cad_files/limb/cache_cable.STEP
60.7 x 46.1 x 12.0 mm

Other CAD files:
hardware/cad_files/lower_body/landing_gear_union_upper_a.stl
hardware/cad_files/legs/rod_connector_cross_block_b.STEP
hardware/cad_files/lower_body/landing_gear_bumper.stl
hardware/cad_files/lower_body/flying_arm_press_left.stl
hardware/cad_files/lower_body/landing_gear_union_lower.stl
hardware/cad_files/main_body/hex_stack_b.STEP
hardware/cad_files/main_body/hex_stack_c.STEP
hardware/cad_files/main_body/hex_stack_d.STEP
hardware/cad_files/main_body/motor_holder_a.STEP
hardware/cad_files/main_body/motor_holder_b.STEP
hardware/cad_files/main_body/motor_holder_c.STEP
hardware/cad_files/main_body/motor_holder_e.STEP
hardware/cad_files/main_body/motor_holder_f.STEP
hardware/cad_files/main_body/motor_holder_h.STEP
hardware/cad_files/main_body/motor_holder_i.STEP
hardware/cad_files/main_body/zip_tie_stack1_a.STEP
hardware/cad_files/main_body/zip_tie_stack1_b.STEP
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

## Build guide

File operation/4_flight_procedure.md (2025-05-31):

# Flight Procedure

⚠️ When flying with the MPC, two persons are required:
- One person flying the drone (on the radio controller)
- One person taking care of the MPC Interface (controlling state machine and MPC command)

> ⚠️⚠️⚠️ The person on the Radio MUST KEEP HIS/HER EYES ON BORINOT AT ALL TIMES ⚠️⚠️⚠️
>
> ⚠️⚠️⚠️ STUDY [EMERGENCY PROCEDURES](#severe-emergency-stop) BEFOREHAND ⚠️⚠️⚠️
>
> ⚠️ The person on the MPC interface should count 3..2..1..0 before sending any command

Refer to the [GUI operation guide](./3_laptop_bringup.md#launch-borinot-graphical-user-interface) to become familiar with the GUI controls and procedures.

**TIP:** If you plan to use the MPC, put the trajectory + goto command directly into the MPC Interface launched on the laptop and restart the mpc launch file. This will save time (and battery) during flight

## Part 1: Radio-controlled flight in Position Control
1. Install the battery
   - Check that the battery is full (~25V)
   - The battery cable should face front and the power cable should point top (see picture)
   - disconnect the power supply
   - Try to position the cables in order to not let them free (and possibily touch a propeller)
   - Attach the battery with the scratch
2. Enable the arm
   - > ⚠️ be sure that nothing can block the arm's motion 
   - Laptop -> MPC interface -> state machine -> Arm -> write `enable` and send request
   - If the arm do not have the correct position, see troubleshoting
3. Move Borinot to the flying area
    - When moving Borinot, grab it from the Pixhawk case (avoid putting your hand in the propeller area)
    - Better to place it to the origin, with the front point to the x direction
    - Check if the pose estimate is converging
      - x ~ 0m
      - y ~ 0m
      - z ~ 0.19m
      - qw ~ 1
      - qx ~ 0
      - qy ~ 0
      - qz ~ 0
4. With the radio controller ⚠️ The drone will fly!! ⚠️ 
    - Set position control:
      - Put the `SWC` switch in the middle position
    - Check Borinot's state:
      - Laptop -> Borinot state GUI -> `PX4: POSITION`
    - Desactivate the KillSwitch (red switch, top position)
    - Arm the drone with the left joystick (pointing down/right)
      -  ⚠️ The motors start spinning
      - Check if the motors are spinning properly, if something weird -> troubleshooting
      - Refer to this [link](https://docs.px4.io/main/en/flight_modes_mc/position.html) image for the command.
    - Take off slowly up
    - ⚠️ Trigger the jump
      - Climb slowly until you see borinot "jumping", then descend when the jump occurs
      - ⚠️ After each arming of Borinot, you have to trigger the jump,
      - After this, you are good to fly
    - If you want to use the MPC, read next part

## To stop the flight 

### Normal stop
At the end of an automatic flight governed by MPC (GoTo command or Trajectory command):
1. Set position control: 
   - Radio, set the `SWC` switch in the down position.
2. Enable the arm,
   - Laptop -> MPC interface -> state machine -> Arm -> write `enable` and send request
3. Land Borinot with the radio,
4. Disable the motors 
   - Radio: left joystick down-left
   - All motors stop
5. ⚠️ Activate the KillSwitch
   - Radio: red switch down
   - The robot is no longer responsive to the radio. This is a safe mode.

### Mild emergency recovery
> ⚠️ QUICK CONTROL RECOVERY ⚠️

You can interrupt any automatic flight and regain control immediately with the radio.
1. Set position control: 
   - Radio: set the `SWC` switch in the down position.
   - The control is transferred from MPC to user
   - The robot will remain in the air in position
2. [Land the robot normally](#normal-stop)
3. ⚠️ Activate the KillSwitch
   - Radio: red switch down
   - The robot is no longer responsive to the radio. This is a safe mode.

### Severe emergency stop
> ⚠️⚠️⚠️ EMERGENCY STOP ⚠️⚠️⚠️
1. ⚠️ Activate the KillSwitch
   - Radio: red switch down
2. ⚠️ All motors will stop.
3. ⚠️ THE ROBOT WILL FALL TO THE GROUND AND CRASH. 

## Part 2: Automatic flight with EAGLE MPC 
1. > ⚠️ **FOLLOW [POSITION CONTROL](#part-1-radio-controlled-flight-in-position-control) 1 TO 4 BEFORE THIS**
   - > ⚠️ Count 3..2..1..0 before sending any command
2. "Stabilize" Borinot in the air with the radio before proceeding further 
3. Enable the MPC `enable`
   - Laptop -> MPC interface -> state machine -> Controller ->  write  `enable` and send request
4. if enabled, arm the mpc with `start` command
   - Laptop -> MPC interface -> state machine -> Controller ->  write  `start` and send request
   - Borinot should stabilize and the arm will strech down, if not -> retake control (using the radio controller, switch to position control by pulling the `SWC` switch down)
5. To use the GoTo Command:
   - The origin is the same as specified for optitrack
   - The frame convention is flu (x: front, y: left, z: up)
6. To use the Trajectory command:
   - > ⚠️ ALWAYS USE RAIL MPC
   - trajectory : select one from `/home/hidro/libraries/eagle_mpc_lib/yaml/borinot_flying_arm_2/trajectories/`
   - warm start : **do not use**
   - mpc : `/home/hidro/libraries/eagle_mpc_lib/yaml/borinot_flying_arm_2/mpc/mpc.yaml`
7. You can lanuch multiple trajectories or goto commands.
8. When done, [stop the robot normally](#normal-stop)

---

| [Top of page](#flight-procedure) | [Back to Operations](./README.md) | [back to Borinot HOME](../README.md) |
| --- | --- | --- |

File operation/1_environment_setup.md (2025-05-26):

# Environment Setup
The following image is the layout of the laboratory flying area. Take it as a reference for the following instructions:
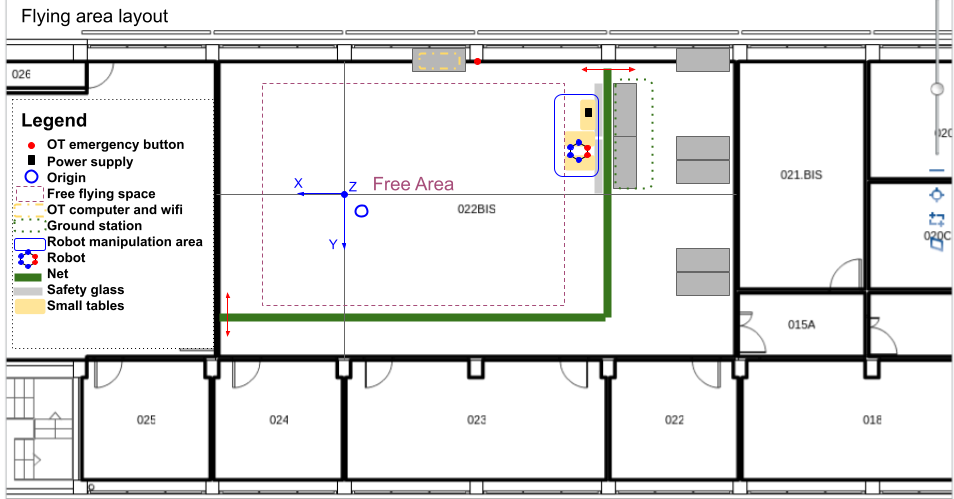
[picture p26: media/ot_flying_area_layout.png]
ot_flying_area_layout


## Part 1: Flying Area Setup
1. Lay down the net using the strings close to the Workshop door.
2. Put the safety glass in front of the Ground Station's desks (should not be covered by the net).
3. Prepare the two tables for borinot manipulation: one leg on each table, the arm in between.
4. Prepare the table for the power supply. Set voltage to 22.5V and current limit to 3.0A.
5. Install the laptop computer in the Ground station.
6. Free the flying area.

## Part 2: OptiTrack Setup
1. Turn on OptiTrack cameras with the siwtch close to the OptiTrack's emergency button.
2. Turn on OptiTrack computer.
3. Take the robot out of the flying area (or put it in the closet).
4. Follow Optitrack calibration. In [iri_optitrack_how_to](https://gitlab.iri.upc.edu/labrobotica/ros/sensors/optitrack/iri_optitrack_how_to) you can find the general calibration method and all the Optitrack documentation. Here there is the basic isntructions to calibrate it for that project:
1. Open Motive. If the space was calibrated one or two days ago, you can open the last configuration. If it's not the case, start the calibration process.
2. Try to remove all the reflections in the area: Press mask visibles, go to a camera with masked points (red). Change view type to MPEG with the right click. See what is creating the reflection and try to remove it covering it or moving the object. Go back to object view with the right click. Unmask and re mask form visible to check if there are more reflections. Repeat until there is nothing more to do.
3. Press start wanding and do it. The wand is on top of the table drawer. For a good calibration each camera must have taken at least 3000 samples.
4. Calibrate. Check if the maximum distance is bigger than 8.0m and the mean error less than 1 mm.
5. Take the ground level marker form the desktop drawer and put it in the origin. The orientation is as shown in the following image (X points to the workshop, Z points to the windows).
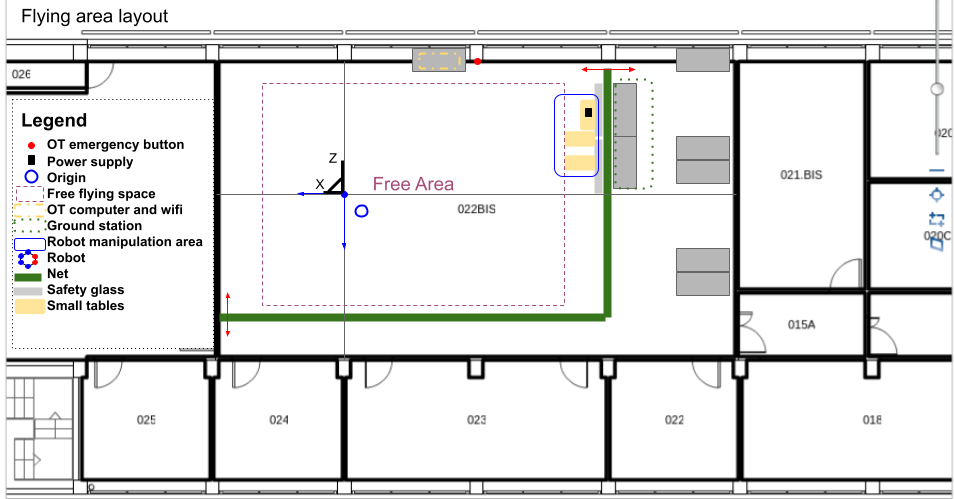
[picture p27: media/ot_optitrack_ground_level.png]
ot_optitrack_ground_level

6. Press ground level calibration.
7. Take the robot to the origin pointing to the wokshop. Check the following image for the robot orientation.
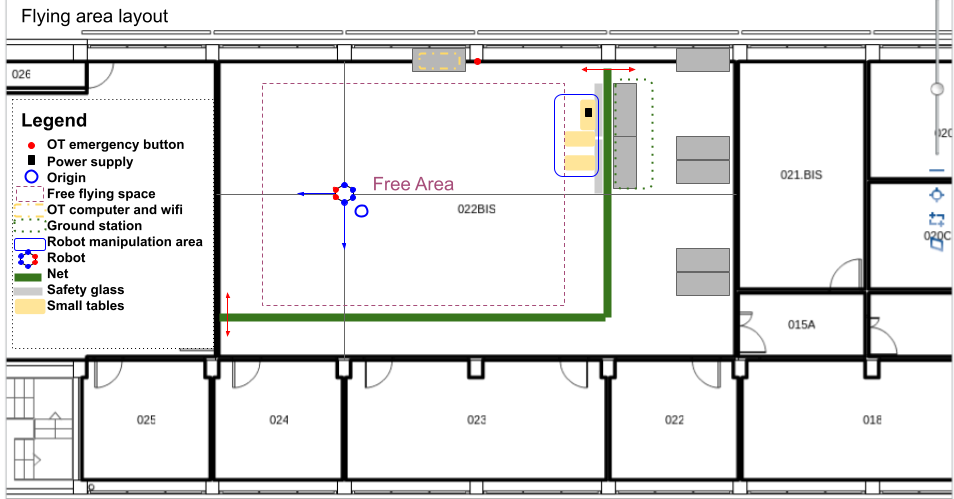
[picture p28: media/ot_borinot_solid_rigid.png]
ot_borinot_solid_rigid

8. Select in motive all the markes and create a solid rigid from selected points. Name the created solid `borinot_fur_ot` which means:
  - name of the robot: borinot
  - reference frame: FUR (X-front, U-up, Z-right) -- see information on reference frames in [architecture](../architecture/README.md#software-for-state-estimation)
  - reference of system: OT: Opti-track
9. Select the center of the solid and the internal rear left marker and with the right click, set pivot point to selected marker.
10. Traslate rigid center to: (check error per markers + untrack markers) --> See [Helper](#helper-optitrack-imu-center-reference-frame) below.
  - x : 62.9 mm
  - y : 29.0 mm
  - z : 84.9 mm
11. Start the stream:
   - Inside Optitrack Streaming Engine:
     - Check that Local interface is `192.168.1.100`, if not, note the new `optitrack_interface` (you will have to modify files inside eagle_ros2) 
     - Check `Broadcast Frame Data`
   - Inside VRPN Streaming Engine:
     - Check that VRPN Broadcast Port is `3883`, if not, not the new `optitrack_port` (you will have to modify files inside eagle_ros2)
     - Check `Broadcast Frame Data`

### **Helper: Optitrack IMU center reference frame**

In Optitrack, follow these steps to set the IMU center reference frame:

1. Select (mouse left-click) the pivot marker in the solid

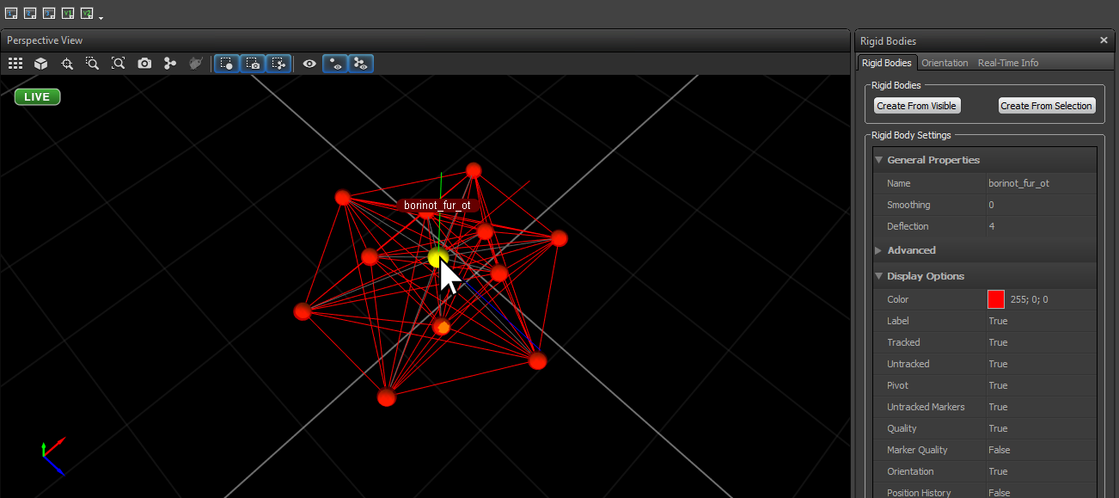
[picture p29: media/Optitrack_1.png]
Optitrack 1
   

2. Also select (SHIFT + mouse left-click) the inner rear-left marker 

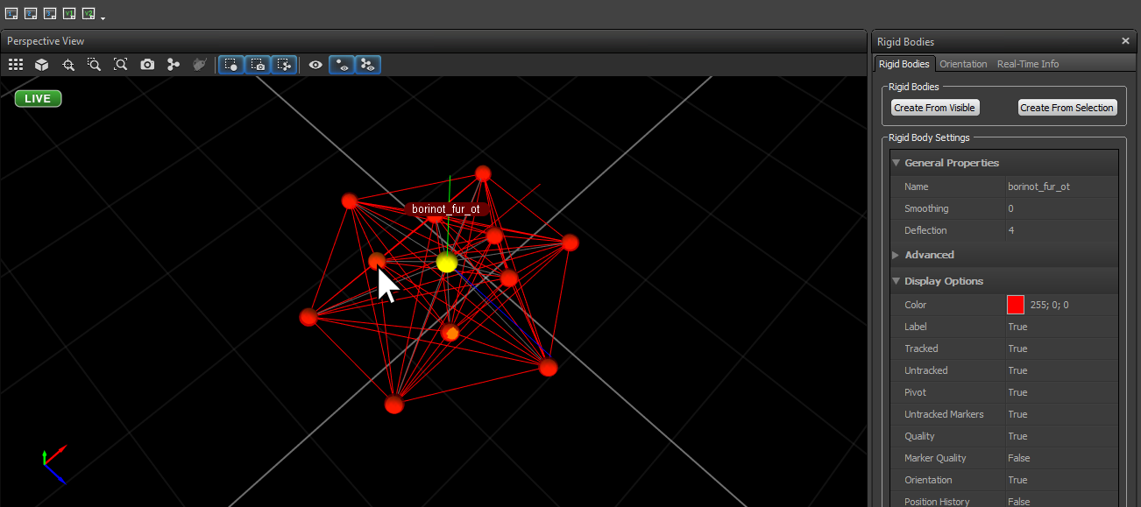
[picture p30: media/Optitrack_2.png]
Optitrack 2
   

1. Set this second marker as pivot point (right-click -> Rigid Body -> Set Pivot Point to Selected Marker)

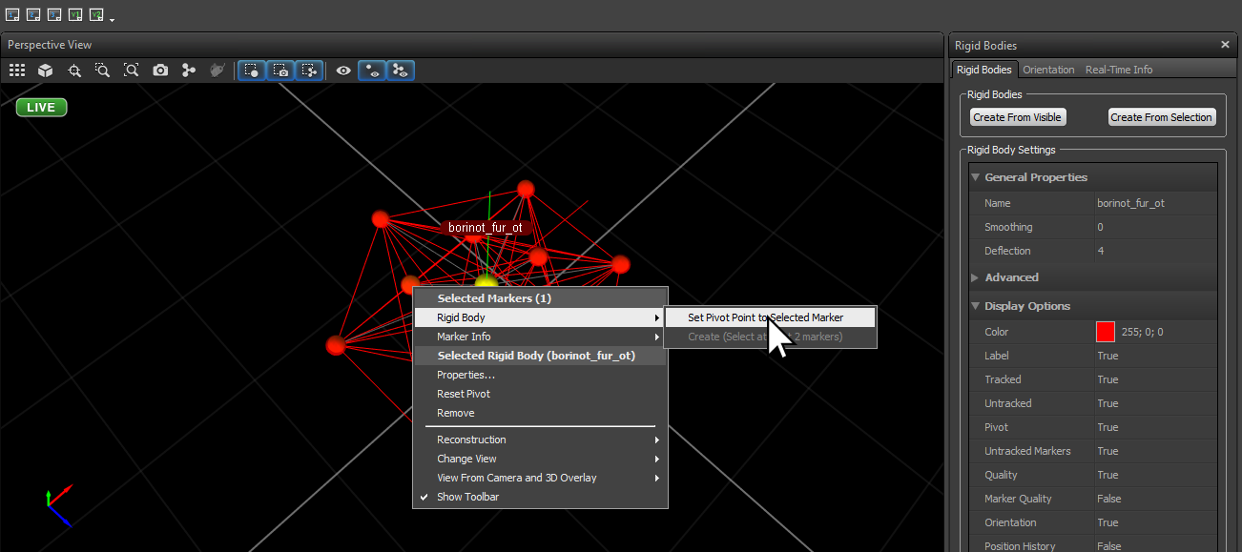
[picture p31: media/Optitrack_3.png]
Optitrack 3
   

   You should see how the pivot moves to the selected marker

1. Select the Orientation tab to add the offsets of the IMU reference frame

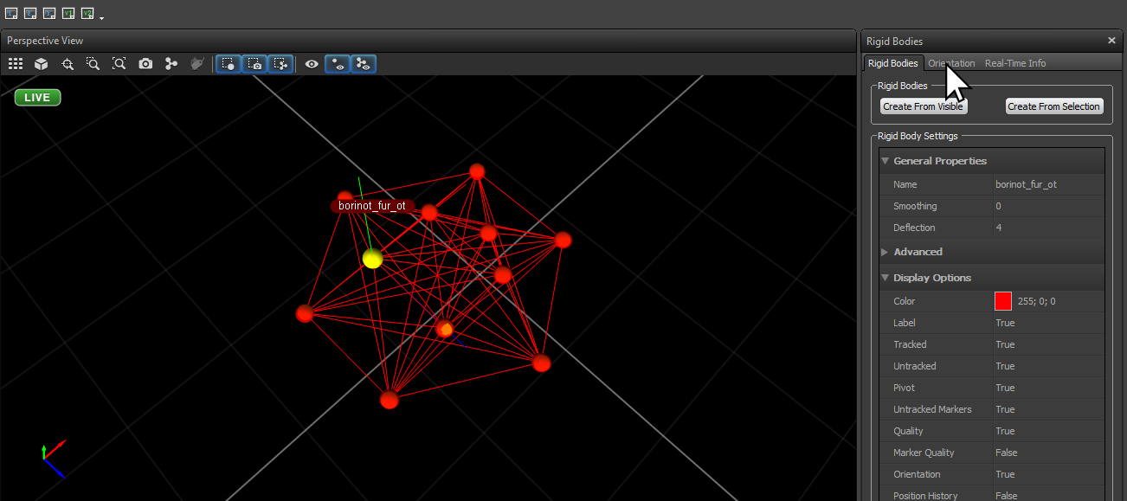
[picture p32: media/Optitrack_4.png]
Optitrack 4
   

5. Insert the XYZ offset values (in mm, not shown) and apply the transformation

   The values are:
      - x : 62.9
      - y : 29.0
      - z : 84.9

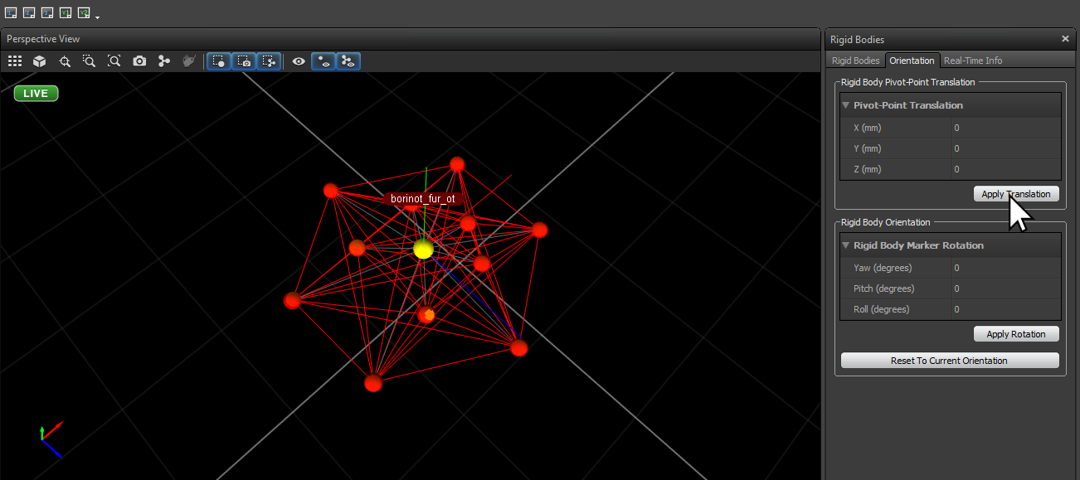
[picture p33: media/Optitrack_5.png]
Optitrack 5
   

   You should see how the pivot moves to the center of the solid, a little above all the other markers.

<!-- # Preflight safety check list

Before each flight, it's important to perform a series of checks to ensure that the UAM is safe to operate. Follow the procedures outlined in the [preflight.md](preflight.md) file to complete these checks.

### Optitrack fusion

The [optitrack.md](optitrack.md) file provides a procedure for fusing the position of the OptiTrack system with the PX4's EKF2 module. -->

---
| [Top of page](#environment-setup) | [Back to Operations](./README.md) | [back to Borinot HOME](../README.md) | [Next → Borinot Bringup](2_borinot_bringup.md) |
| --- | --- | --- | --- |

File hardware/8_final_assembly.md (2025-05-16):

# Final Assembly

## Part 1: Lower Body Mounting

### Materials
- Lower Body
- Upper Body
- Screws M3 flat head 25mm x8

### Steps

1. Put the upper body on his back (upside-down)
> :information_source: The wifi antenna can be fold
2. Put the lower Body on top of the upper body 
> ⚠️  The orientation of the arm should match the orientation of the drone
3. Screw the structure together
4. 
## Part 2: ODRI Wirering

### Steps

1. Connect the uDriver power cables together 
2. Connect the Master Board power cables together 
3. Connect the ethernet cable to the masterboard

[Return to Hardware Building Instructions](README.md)
[Next → Software Setup](../software/README.md)

---
| [Top of page](#final-assembly) | [Back to Hardware Building Instructions](README.md) | [Back to Borinot HOME](../README.md) |
| --- | --- | --- |

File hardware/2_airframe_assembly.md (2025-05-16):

# Airframe Assembly Guide

The airframe is the structure that houses and maintains the motors in their respective positions. This guide covers the assembly procedure for the airframe.

---

## Part 1: Motor Case Preparation

The Motor Case holds both the motor and the carbon fiber tubes together. It also houses the esc and the Optitrack markers.

### Materials

Exploded view of Motor Case

> **Exploded View: Motor Case components (all 3D printed parts)**

| Part Name | Quantity | Description | Reference |
|---|:---:|---|---|
| Motor Cases | 6 | 3D parts – Motor Holder | [CAD](CAD/platform/) |
| M4 Marker | 6 | 14 mm M4 | [Optitrack](https://optitrack.com/accessories/markers/#mcm-14.0-m4-10) |
| M4 Nuts | 6 | M4 | |
| M4 Screws | 6 | M4x10mm Nylon | |
| M3 Inserts | 12 | M3 | |

### Steps

1. **Clean** all Motor Case components, ensuring removal of any support material inside the tube holder.  
   > ⚠️  Use a drill if anomalies are found inside the tube holder.

Before marker assembly Before marker assembly

> **Side view:** middle part before and after installing the marker

2. **Assemble** the marker (M4 nut + M4 nylon screw + M4 marker) according to the **Motor ID**.  
   > ⚠️  The faces of the middle part are not symmetric. Test alignement with the top and bottom parts so find the correct orientation.

   > :information_source: Each Motor Case is identified using the [Hexarotor X airframe reference](https://docs.px4.io/main/en/airframes/airframe_reference.html#hexarotor-x) ID.

Marker position

> **Side view** Marker position

| Motor ID | Marker Position |
|:---:|---|
| 1 | Bottom Right |
| 2 | Top Right |
| 3 | Top Left |
| 4 | Bottom Left |
| 5 | Top Right |
| 6 | Bottom Right |

Before asserts on bottom After asserts on bottom

> **Side view:** Bottom part before and after inserting asserts

3. **Install** two inserts on the bottom part.

Cover assembly before Cover assembly after

> **Side view:** Cover before and after assembling the cover

4. **Assemble** the different piece composing the cover.

5. **Repeat** these steps for all 6 Motor Cases.

Motor case prepared

> **Side view:** Motor case prepared.

---

## Part 2: Frame Assembly

The frame is composed of two intersecting triangles. Each motor case is a vertex and each carbon fiber tube a edge.

### Materials

| Part Name | Quantity | Description | Reference |
|---|:---:|---|---|
| Carbon Fiber Tubes | 6 | ø8mm x 352.5mm, Round Checked | [McMaster](https://www.mcmaster.com/products/carbon-fiber-tubing/) |
| O-ring Seals | 24 | ø8 mm | [TheORingStore](https://www.theoringstore.com/store/) |
| M3x30mm Screws | 24 | M3x30mm | |
| M3x05mm Screws | 12 | M3x05mm | |
| Motors and ESCs | 6 | | [Component Preparation](1_component_preparation.md) |

Assembled airframe top view

> **`Assembled Airframe:`** Top view of the assembled airframe

| Motor ID | Left Position | Right Position |
|:---:|---|---|
| 1 | Middle | Top |
| 2 | Middle | Top |
| 3 | Top | Bottom |
| 4 | Top | Bottom |
| 5 | Bottom | Middle |
| 6 | Bottom | Middle |

### Steps

Motor Case 3 assembly

> **`Assembly Step 1:`** Top view of Motor Case 3 assembly

1. **Combine Motor Cases:** Assemble the top, middle, and bottom parts of each Motor Case.  
   > :information_source: Ensure the O-rings are snugly fitted.
2. **Attach Tubes:** Insert Carbon Fiber Tubes into the tube holders of the Motor Cases and secure them with 4 M3x30mm screws.  
   > ⚠️  Refer to the table above for tube positioning.
3. **Add Tube Accessories:** For each tube, slide on two O-rings and a 7cm length of heat shrink tubing on both ends.
4. **Assemble Triangles:**  
   - Assemble Motor Cases 1, 3, and 6 to form the first triangle.  
   - Assemble Motor Cases 4 and 5 to form the second triangle.
5. **Merge Triangles:** Merge the two triangles before sealing the final Motor Case (Motor Case 2).
6. **Finalize Frame:** Complete the assembly by installing Motor Case 2.

Frame before closing

> **`Frame Finalization:`** Top view of the airframe before closing

---

## Part 3: Finalizing Assembly

With the frame assembled, install the ESCs and connect them to the motors. Route the ESC cables through the designated heat shrink tubing for stability and a clean finish.

### Materials

Assembled airframe

> **`Reference:`** Assembled airframe used as a reference for ESC installation

### Steps

1. **Install ESCs:** Position the ESC within the bottom section of each Motor Case and connect it to its corresponding motor.
2. **Mount Covers:** Attach the cover onto each Motor Case using 2 M3x5mm screws.
3. **Route Cables:** Route the ESC cables through the designated heat shrink tubing on the Carbon Fiber Tubes.  
   > ⚠️  Ensure cables are routed according to the assembly guidelines.
4. **Repeat:** Complete these steps for all 6 Motor Cases.

---

| [Top of page](#airframe-assembly-guide) | [Back to Hardware Building Instructions](README.md) | [Back to Borinot HOME](../README.md) | [Next -> go to Main Body Assembly](./3_main_body_assembly.md)
| --- | --- | --- | --- |

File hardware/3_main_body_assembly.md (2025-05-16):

# Borinot: Upper Body Assembly Guide

Top view of the assembled upperbody

> *Assembled Upper Body, [**weight**] g*
<!-- Make sure to provide the actual weight once known -->

The Upper Body of Borinot acts as a flying platform, similar to a hexacopter. It consists of the main body which accommodates core electronics like the onboard NUC computer, the Pixhawk flight controller, and the power module, as well as the airframe that ensures the stable positioning of the motors. The Upper Body can operate as a standalone hexacopter or be integrated into the Lower Body for expanded functionalities.

---

## Components list

| Part Name | Quantity | Description | Reference |
|:-|:-:|:-|:-:|
| Main Body Case | 1 | 3D parts - Stack | [CAD](CAD/platform/) |
| NUC | 1 | NUC Kit NUC7i7DNKE | [intel](https://ark.intel.com/content/www/us/en/ark/products/130392/intel-nuc-kit-nuc7i7dnke.html) |
| Pixhawk 5x | 1 | Flight Controller | [Holybro](https://holybro.com/products/pixhawk-5x?variant=40842119839933) |
| Ethernet Converter | 1 | [**Specify dimension**] | [**Specify Link**] |
| USB C Cable | 1 | [**Specify dimension**] | [**Specify Link**] |
| Wi-Fi Antenna | 1 | Wi-Fi Antenna | [**Specify Link**] |
| Radio Receiver | 1 | Radio | [RC Innovations](https://rc-innovations.es/shop/FS-iA6B-receptor-6-canales-telemetria-flysky) |
| Damper | 10 | For Pixhawk | [**Specify Link**] |
| M3 Nuts | 16 | Hex, M3 | [RS](https://uk.rs-online.com/web/p/hex-nuts/0198318) |
| M3 6mm Screws | 4 | M3x6mm | [RS](https://uk.rs-online.com/web/p/socket-screws/0281372) |
| M3 10mm Screws | 4 | M3x10mm | [RS](https://uk.rs-online.com/web/p/socket-screws/0281394) |
| M3 16mm Screws | 4 | M3x16mm | [RS](https://uk.rs-online.com/web/p/socket-screws/0292423) |
| Long Carbon Fiber Tubes | 4 | 5mmx3mmx150mm, Square | [McMaster](https://www.mcmaster.com/products/carbon-fiber-tubing/) |
| Short Carbon Fiber Tubes | 2 | 5mmx3mmx65mm, Square | [McMaster](https://www.mcmaster.com/products/carbon-fiber-tubing/) |
| Airframe | 1 | Assembled structure | [Airframe Assembly Guide](airframe.md) |
| Power Module | 1 | Essential power component | [Power Module Modification Guide](power_module.md) |

> ⚠️  Please note that While the Pixhawk 5x has been discontinued, the Pixhawk 6x is mechanically compatible. However, Ensure software compatibility before proceeding.

## Assembly

### Prerequisite: Component Preparations

Before starting the assembly of the upper body, ensure that:

1. The power module has been modified following the [Power Module Modification Guide](power_module.md).
2. The airframe has been assembled following the [Airframe Assembly Guide](airframe.md).

### Part 1: Main Body Case Preparation

Ensure the main body case and associated components are ready for assembly:

- **Clean the 3D printed parts.** Ensure there are no residual supports or anomalies.
    > ⚠️  Pay special attention to the marker holders and fastener holders.





- **Install the M3 nuts and dampers onto the Pixhawk case.**
- **Insert the 65mm square carbon fiber tubes into the Pixhawk case.**
- **Attach the battery support to the Pixhawk case using M3 10mm screws.**




- **Position the M3 nuts and dampers on the top part of the main body case.**




- **Place the M3 nuts on the bottom part of the main body case.**

### Part 2: Main Body Assembly

The main body requires careful placement and connection of components:

- **Attach the Wi-Fi antenna to the Pixhawk case using fasteners.**




- **Mount the power module onto the top part of the main body using 4 M3 6mm screws.**
- **Secure the Ethernet adapter and radio receiver to the top part using fasteners.**




- **Place the Pixhawk 5x inside its designated case.**
- **Guide the cables of the Pixhawk and the antenna through the corresponding holes in the top part.**
- **Secure the Pixhawk case to the top part using fasteners.**
- **Connect the NUC to the power module using the designated computer cable.**
- **Connect the NUC to the Wi-Fi antenna.**
- **Position the bottom part of the main body inside the contour part.**
- **Insert the 150mm square carbon fiber tubes into the top and bottom parts of the main body case.**



- **Place the NUC inside the main body case and secure it to the bottom part using 4 M3 16mm screws.**
- **Connect all necessary cables**:
  - **Pixhawk 5x Ethernet to the NUC.**
  - **Pixhawk 5x power to the power module.**
  - **Pixhawk 5x USB to the NUC using the provided USB C cable.**

Ensure all connections are secure before proceeding with the next step.

---

| [Top of page](#main-body-assembly-guide) | [Back to Hardware Building Instructions](README.md) | [Back to Borinot HOME](../README.md) | [Next → Upper Body Integration](4_upper_body_integration.md) |
| --- | --- | --- | --- |

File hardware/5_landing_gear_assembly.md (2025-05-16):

# Borinot: Landing Gear Assembly Guide

Side view of the assembled landing gear
<!-- Need picture of the assembled landing gear, maybe from above-->

> *Assembled Landing Gaer, [**weight**] g*
<!-- Fill in the weight -->

The landing gear serves as the foundational structure for Borinot's lower body, ensuring safe and stable landings. It comprises support tubes, connectors, and rubber seals. This guide outlines the detailed assembly process for the landing gear.

---

## Components List

| Part Name | Qty. | Description | Reference |
|---|:---:|---|---|
| [3D Kit](CAD/legs/) | 1 | Landing Gear | [Link](CAD/legs/) |
| Ø20mm O-Ring Seals | 12 | Rubber seals | - |
| M3x10mm Screws | 8 | - | - |
| M3x16mm Screws | 8 | - | - |
| M3 Nuts | 16 | - | - |
| Ø8x6x110mm CF Tubes | 4 | Carbon tubes | - |
| Ø8x6x170mm CF Tubes | 2 | Carbon tubes | - |
| Ø8x6x300mm CF Tubes | 2 | Main support tubes | - |

## Assembly/Modification Guide

### Part 1: 3D Kit Preparation

- **Clean all components of the Landing Gear - 3D Kit ensuring that the tube entry points are devoid of any obstructions**.

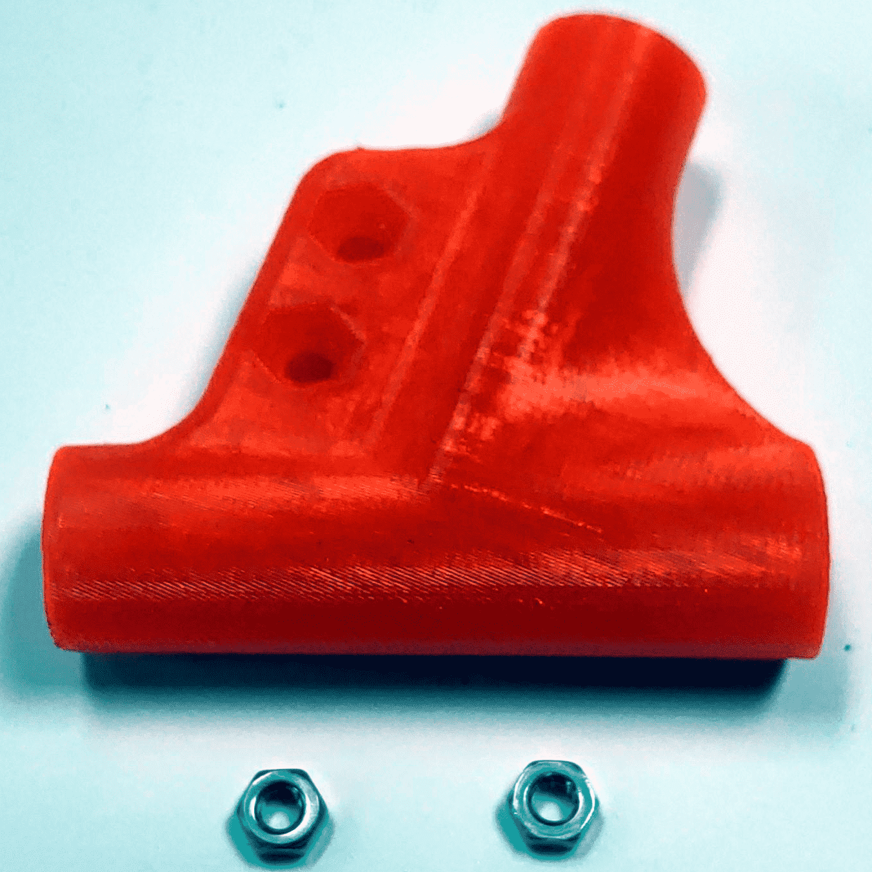
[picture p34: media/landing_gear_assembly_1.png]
Side view of the assembled landing gear

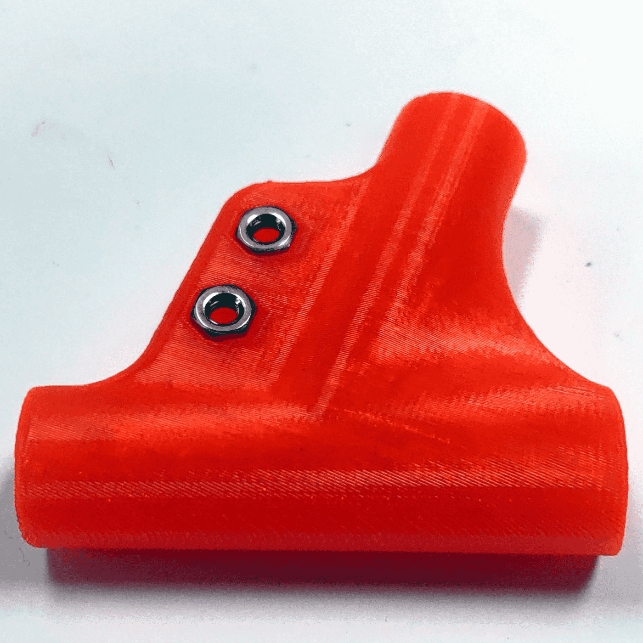
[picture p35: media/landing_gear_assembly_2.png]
Side view of the assembled landing gear


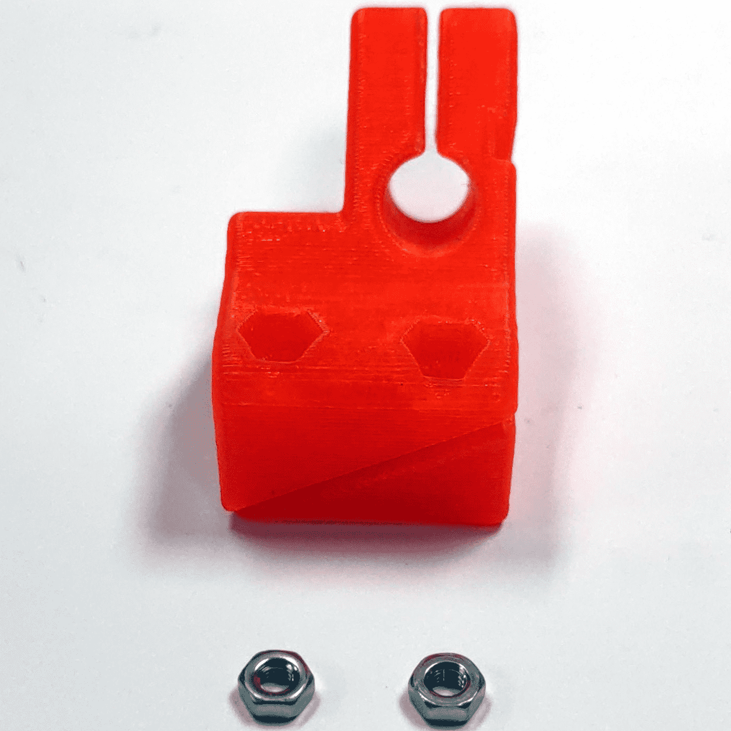
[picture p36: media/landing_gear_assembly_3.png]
Side view of the assembled landing gear

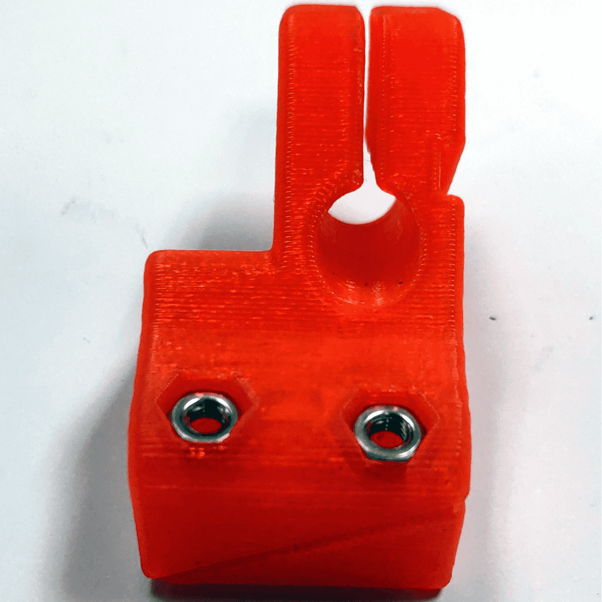
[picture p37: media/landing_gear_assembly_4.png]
Side view of the assembled landing gear


- **Insert M3 Nuts into the designated slots**.

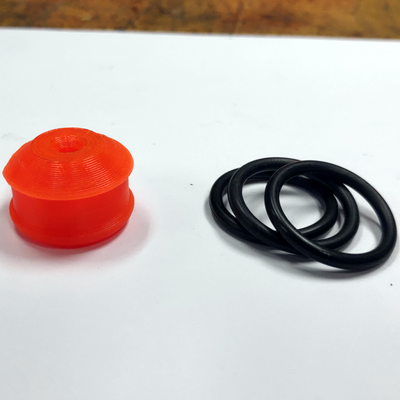
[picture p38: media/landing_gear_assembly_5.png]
Side view of the assembled landing gear

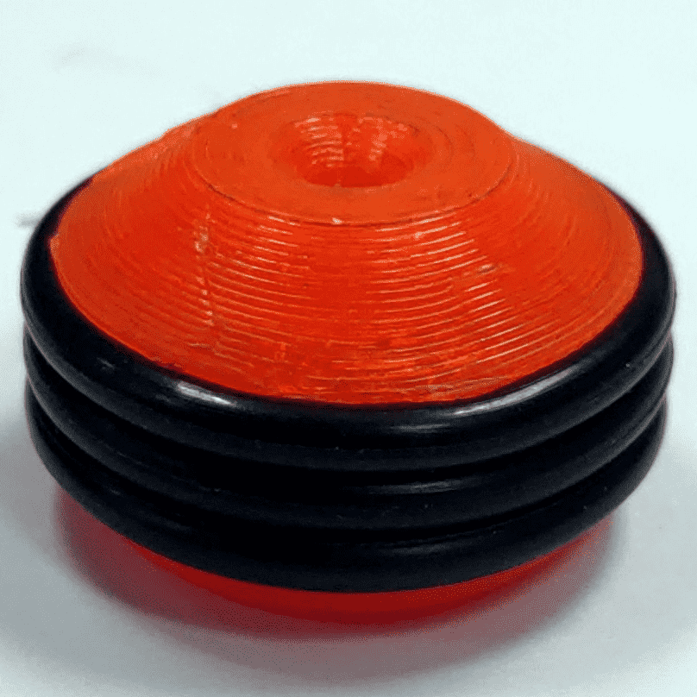
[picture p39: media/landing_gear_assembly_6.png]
Side view of the assembled landing gear


- **Position 3 Ø20mm O-Ring Seals around each pawn for cushioning**.

### Part 2: Assembly

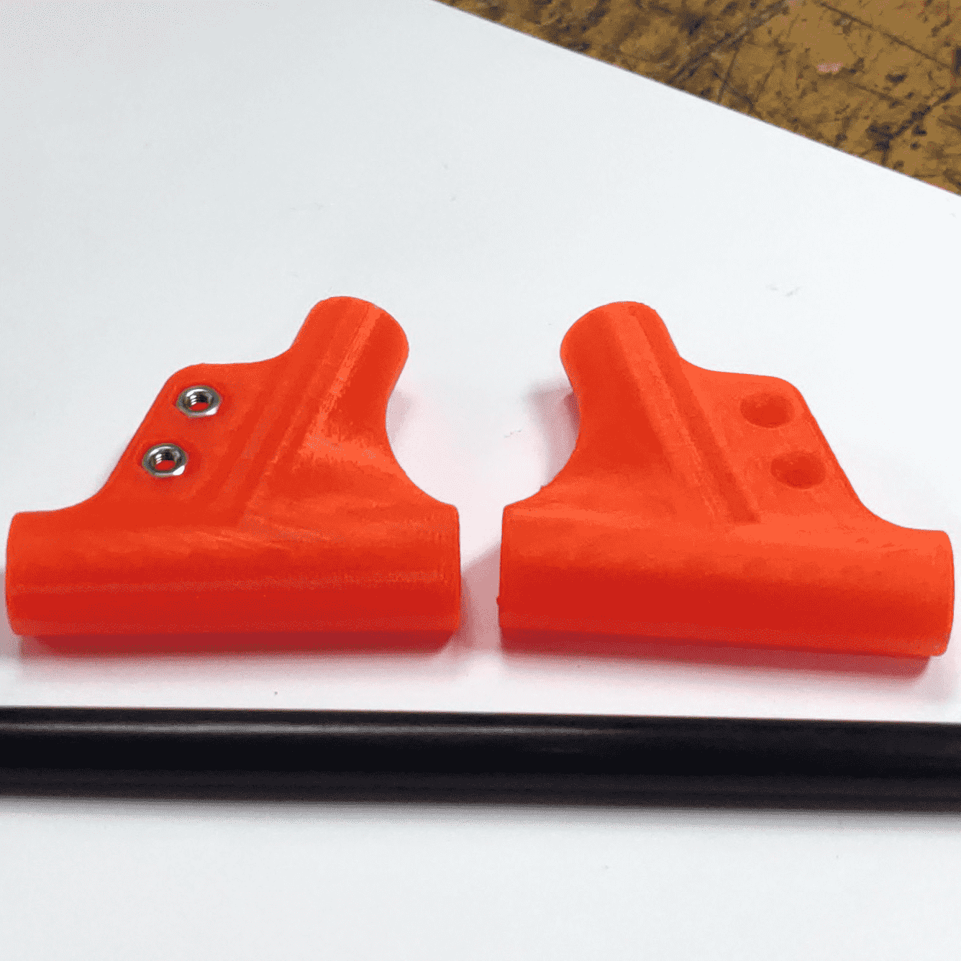
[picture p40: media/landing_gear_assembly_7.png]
Side view of the assembled landing gear

Side view of the assembled landing gear

- **Connect the wye connectors to the pawns using the 300mm carbon fiber tubes. Ensure alignment as shown in the reference images. Repeat for the second set**.

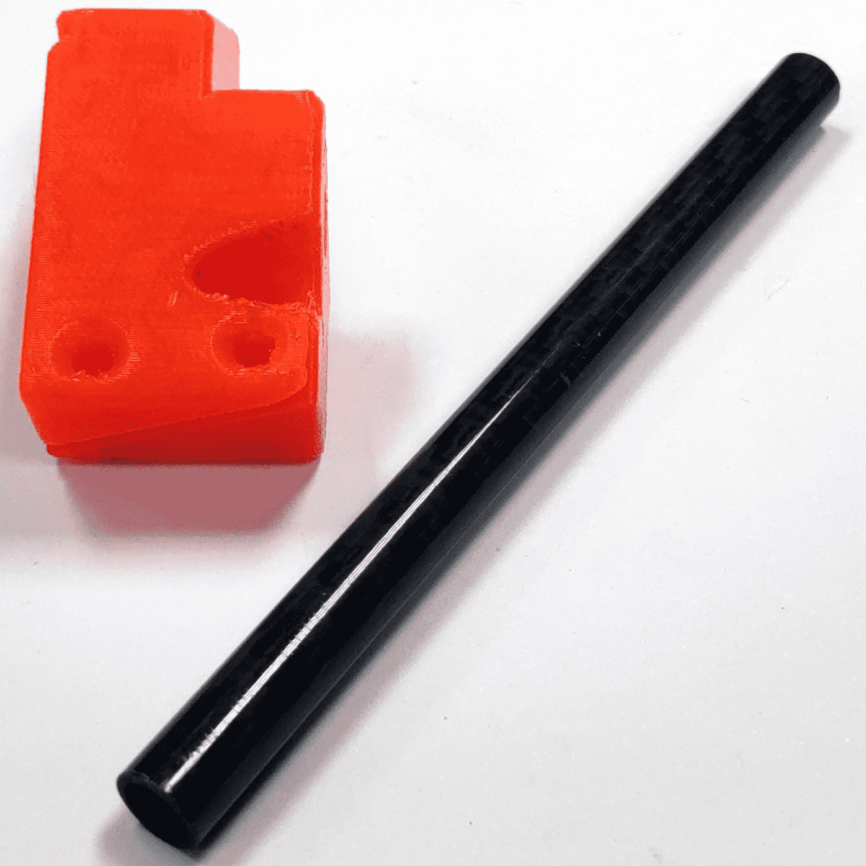
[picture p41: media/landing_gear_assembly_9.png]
Side view of the assembled landing gear

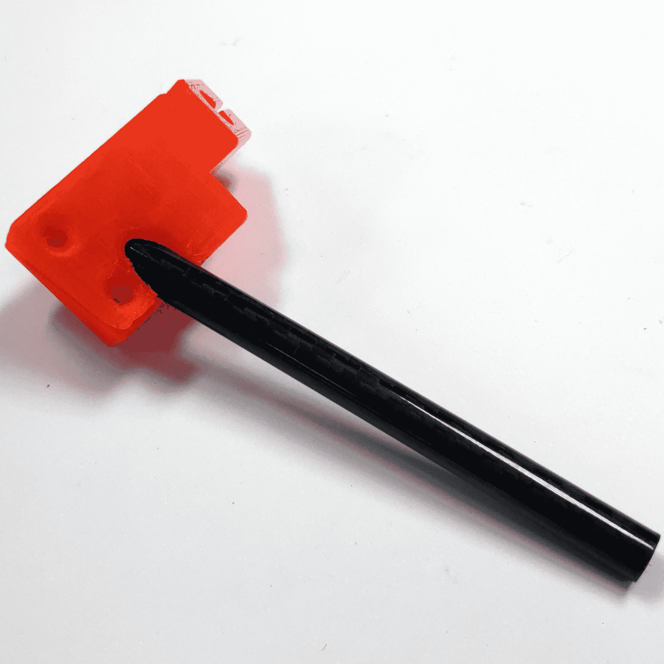
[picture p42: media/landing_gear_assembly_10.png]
Side view of the assembled landing gear


- **Join the cross-block connectors using the 170mm carbon fiber tubes, ensuring alignment with provided images. Create two such assemblies**.

Side view of the assembled landing gear
Side view of the assembled landing gear

- **Assemble the entire landing gear by integrating the previously made assemblies with the 4 110mm carbon fiber tubes. Follow the reference images for accurate alignment**.

Side view of the assembled landing gear
Side view of the assembled landing gear

## Landing Gear Assembly

#### Components List

| Part Name | Quantity |
|:-:|:-:|
| [Landing Gear - 3D Kit](CAD/legs/) | 1 |
| Ø20mm O-Ring Seals | 12 |
| M3x10mm Screws | 8 |
| M3x16mm Screws | 8 |
| M3 Nuts | 16 |
| Ø8mmx6mmx110.0mm Carbon Fiber Round Checked Tubes | 4 |
| Ø8mmx6mmx170.0mm Carbon Fiber Round Checked Tubes | 2 |
| Ø8mmx6mmx300.0mm Carbon Fiber Round Checked Tubes | 2 |

#### 3D Preparation

1. Clean all components of the **Landing Gear - 3D Kit**. Ensure that tube entry points are clear of any obstructions.
2. Insert **M3 Nuts** in their specified slots.
3. Place 3 **Ø20mm O-Ring Seals** around each pawn.

#### Assembly

1. Join the wye connectors and pawns with the 300mm carbon fiber tubes. Ensure alignment with provided pictures (or diagrams). Repeat the step for the second set.
2. Combine the cross-block connectors with the 170mm carbon fiber tubes, following reference images. Create two such assemblies.
3. Integrate the entire setup using the 4 110mm carbon fiber tubes, ensuring alignment with provided pictures (or diagrams).

---

| [Top of page](#borinot-landing-gear-assembly-guide) | [Back to Hardware Building Instructions](README.md) | [Back to Borinot HOME](../README.md) | [Next → Flying Arm Assembly](6_flying_arm_assembly.md) |
| --- | --- | --- | --- |

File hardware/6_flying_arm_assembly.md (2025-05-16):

# Borinot: Flying Arm Assembly Guide

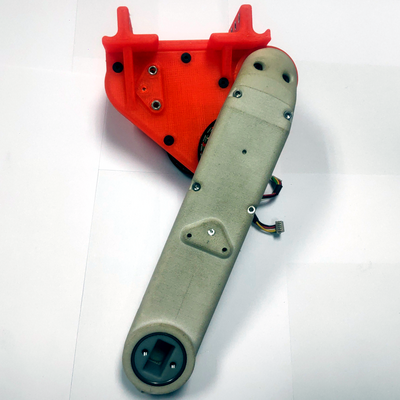
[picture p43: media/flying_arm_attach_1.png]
Top view of the assembled flying arm


> *Assembled Flying Arm, [**weight**] g*
<!-- Fill in the weight -->

The flying arm is a critical component of Borinot, responsible for the robot's diverse range of movements and functionalities. It serves multiple roles: as a tail for aerial locomotion, a hand for agile aerial manipulation, and even as a leg for hybrid aerial-contact locomotion. Comprising two links and an extremity, this guide will walk you through the assembly process.
> **Note**: Both links are based on the actuator module from the [Open Dynamic Robot Initiative (ODRI)](https://github.com/open-dynamic-robot-initiative/open_robot_actuator_hardware/blob/master/mechanics/actuator_module_v1/actuator_module_v1.1.md). Refer to their project for additional information.

---

## Components List

| Part Name | Quantity | Description | Reference |
|---|:---:|---|---|
| Extremity - 3D Kit | 1 | 3D printed component for extremity | [Link to the part](CAD/limbs/) |
| Flying link - 3D Kit | 1 | 3D printed link component | [Link to the part](CAD/limb/) |
| Off-the-shelf Components | 2 | Components used within the links | [ODRI Actuator Components](https://github.com/open-dynamic-robot-initiative/open_robot_actuator_hardware/blob/master/mechanics/actuator_module_v1/actuator_module_v1.1.md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) |
| M3x5mm Flat Head Screws | 7 | - | - |
| M3x15mm Screw | 4 | - | - |
| M3x16mm Flat Head Nylon Screw | 2 | - | - |
| M3x20mm Flat Head Screws | 6 | - | - |
| M3 Nuts | 18 | - | - |
| M3 Inserts | 5 | - | - |

## Assembly

### Prerequisite: ODRI Actuator Module and Motor & Encoder Preparation

Top view of the assembled first link
Side view of the motor and encoder of the base link

As previously mentioned, the flying arm consists of two links: The base link, which is a variant of the actuator module, and the first link, which mirrors the [ODRI Actuator Module V1.1](https://github.com/open-dynamic-robot-initiative/open_robot_actuator_hardware/blob/master/mechanics/actuator_module_v1/actuator_module_v1.1.md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). Begin by assembling a complete actuator module based on the ODRI guide, and then prepare the components for the base link.

### Part 1: Base Link's Shell Preparation

Prepare the base link's shell to accommodate the components you've prepared (the motor and encoder).

Exploded view for base link shell

- **Thoroughly clean the Flying - 3D Kit components**.
- **Insert the M3 Nuts, M3 Inserts, Output Bearings, and Transmission Bearings into their respective slots in the 3D kit components**.

### Part 2: Base Link Assembly

The base link shares components with the actuator module, so the assembly process is quite similar.

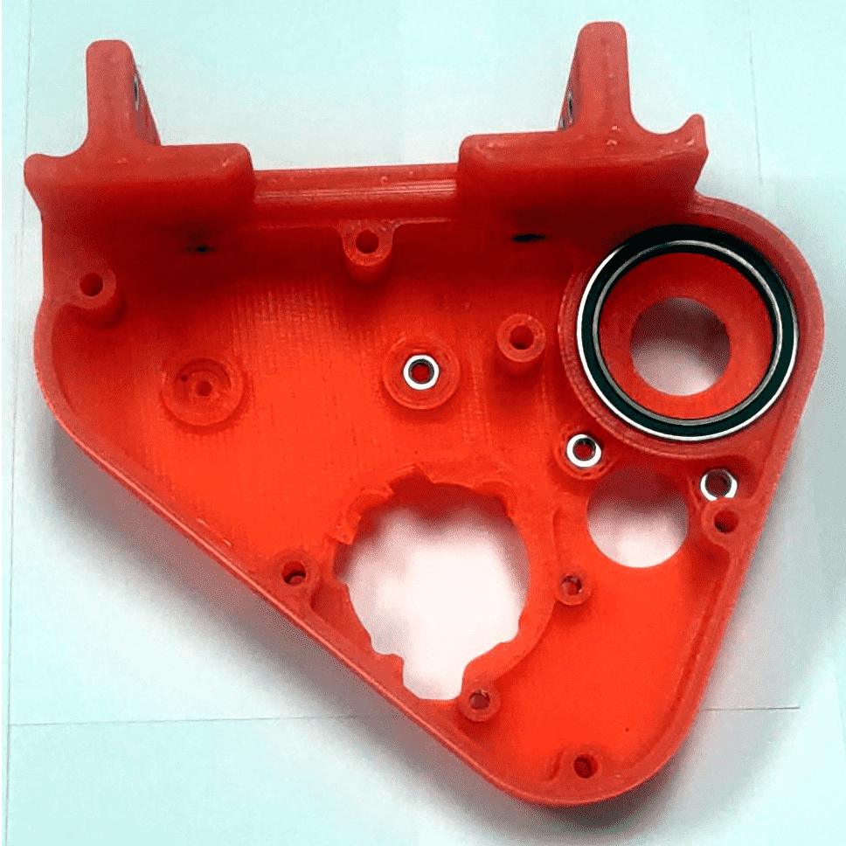
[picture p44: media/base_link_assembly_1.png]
Top view base link assembly (1)

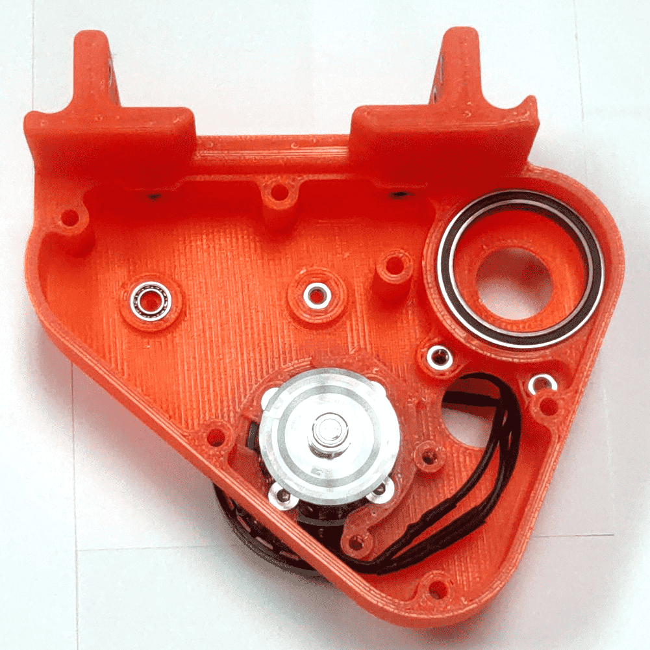
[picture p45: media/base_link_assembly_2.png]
Top view base link assembly (2)

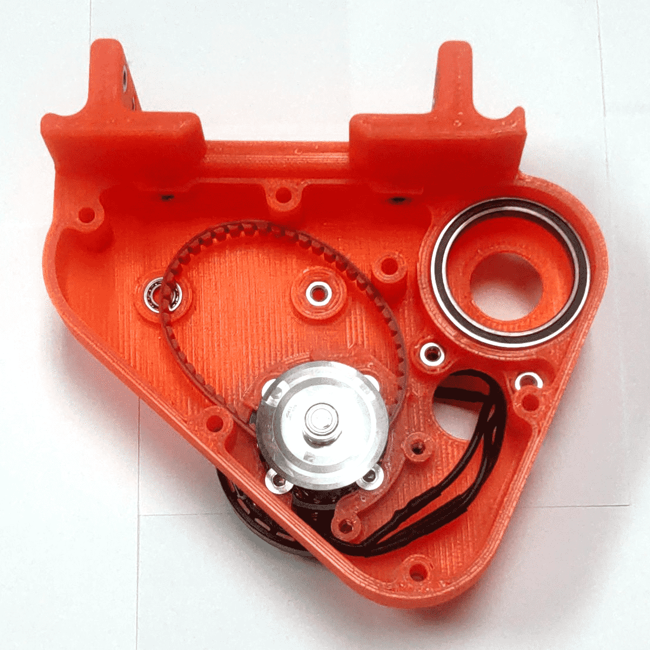
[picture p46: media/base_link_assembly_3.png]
Top view base link assembly (3)

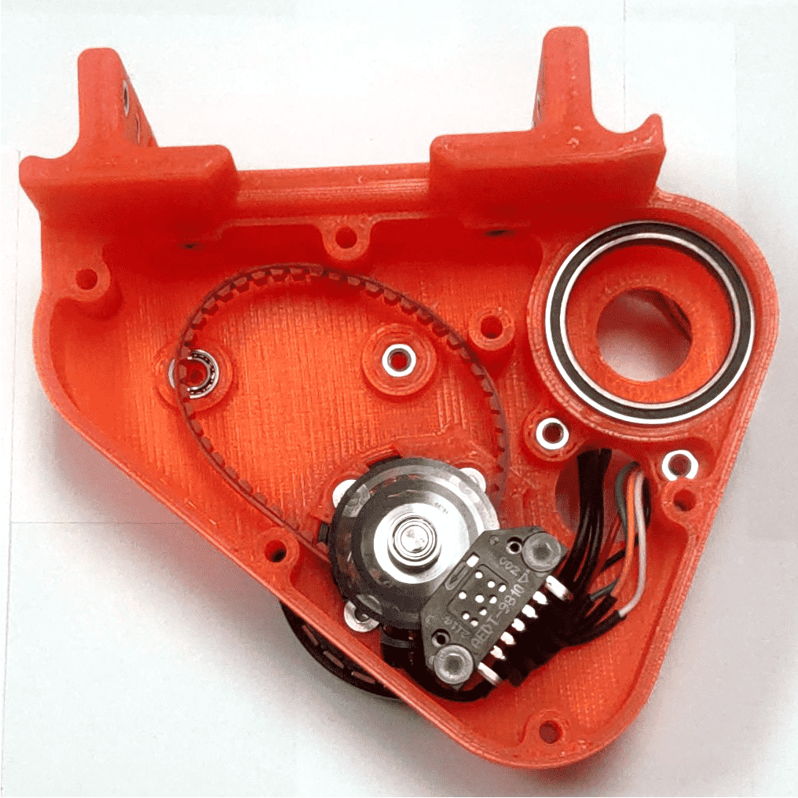
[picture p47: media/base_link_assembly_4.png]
Top view base link assembly (4)

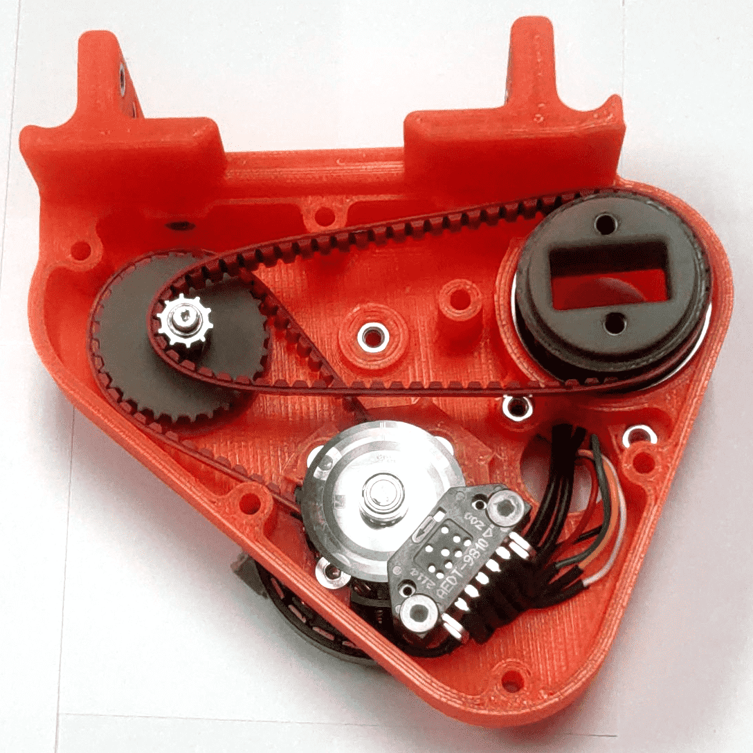
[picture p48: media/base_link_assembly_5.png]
Top view base link assembly (5)

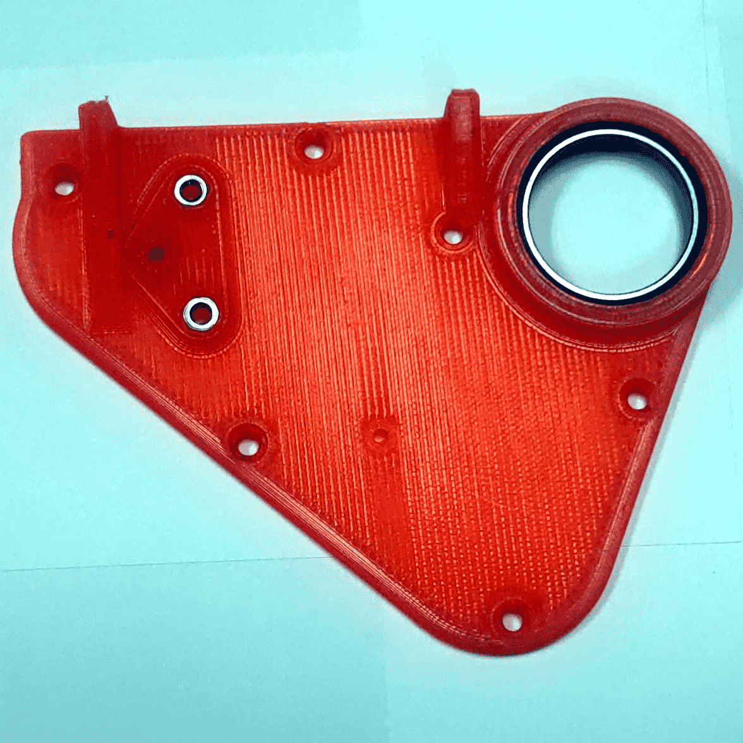
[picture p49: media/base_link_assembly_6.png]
Top view base link assembly (6)


- **Secure the motor within Shell A using 4 screws**.
- **Position the 150mm timing belt around the motor's axle**.
- **Secure the encoder next to the motor using nylon screws**.
- **Align the ODRI 3D component with the 201mm timing belt and close using the Flying Case B secured with 6x20mm screws**.

### Part 3: Link Attach

With both the base and first link assembled, the final step involves connecting them with the extremity.

- **Route the first link's cable through the base link**.
- **Attach the first link and the base link using 2 M3 15mm screws**.

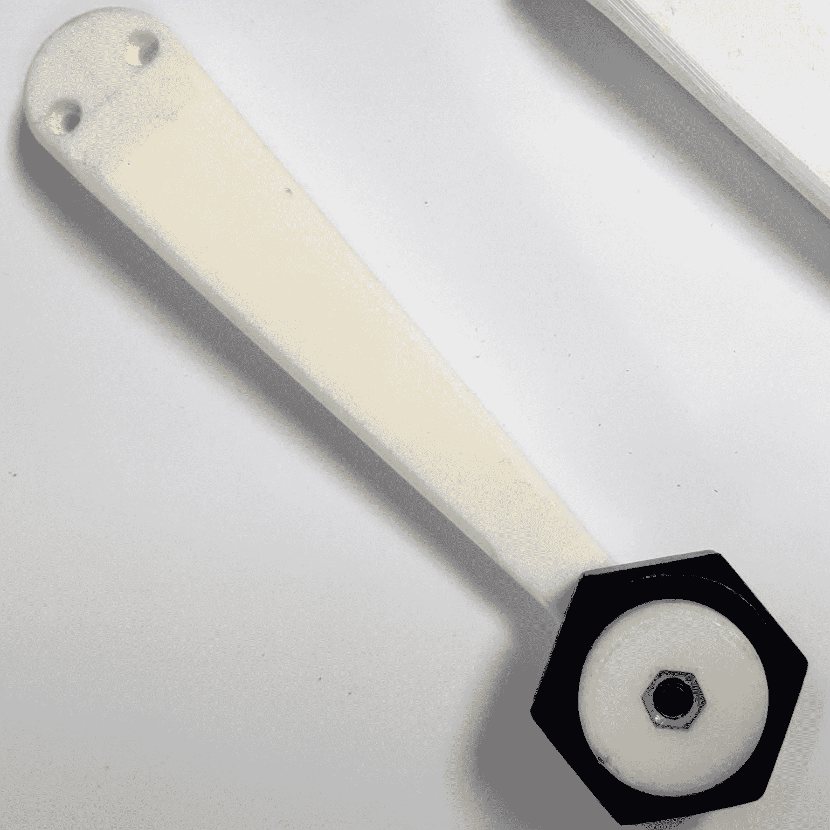
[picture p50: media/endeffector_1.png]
Top view for extremity (1)

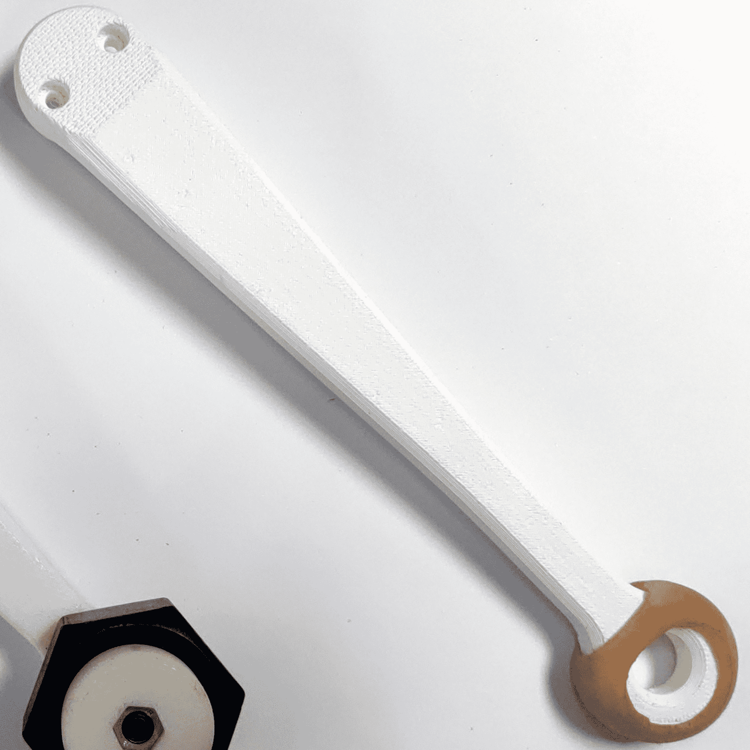
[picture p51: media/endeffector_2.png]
Top view for extremity (2)


- **Attach the ODRI link and the extremity using 2 M3 15mm screws**.

<!-- Add section for the extremities -->

## ODRI Controller Assembly

#### Components List

| Part Name | Quantity |
|:-:|:-:|
| [Controller Case - 3D Kit](CAD/platform/) | 1 |
| Master Board | 1 |
| Micro Driver | 1 |
| M2 Nuts | 4 |
| M2.5 Nuts | 4 |
| M3 Inserts | 3 |
| M3x5mm Screws| 3 |
| M2x6mm Screws | 4 |
| M2.5x6mm Screws | 4 |

#### 3D Preparation

1. Clean all parts of the **Controller Case - 3D Kit**.
2. Insert **M2 Nuts**, **M2.5 Nuts**, and **M3 Inserts** in their designated slots in the 3D kit components.

#### Assembly

1. Secure the master board inside the controller case - top using M2 screws.
2. Mount the micro driver at the bottom of the controller case, securing with M2.5 screws.
3. Connect the two links to the micro driver. Ensure the cable routes through the designated holes in both the controller and flying cases.
4. Establish a connection between the micro driver and the master board. Close the assembly using 3 M3 screws.

### Arm Assembly - Extremity

#### Components List

| Part Name | Quantity |
|:-:|:-:|
| [Extremity - 3D Kit](CAD/limbs/) | 1 |

1. Thoroughly clean the extremity part.

### Arm Assembly - ODRI Link

Refer to the [actuator module page](https://github.com/open-dynamic-robot-initiative/open_robot_actuator_hardware/blob/master/mechanics/actuator_module_v1/README.md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) of the ODRI project for assembly details.

### Arm Assembly - Flying Link

#### Components List

| Part Name | Quantity |
|:-:|:-:|
| [Flying link - 3D Kit](CAD/limb/) | 1 |
| Output Bearings | 2 |
| Transmission Bearings | 3 |
| M3x5mm flat head Screws | 4 |
| M3x15mm Screw | 4 |
| M3x16mm Flat Head nylon Screw | 2 |
| M3x20mm flat head Screws | 6 |
| 201mm timing belt | 1 |
| 150mm timing belt | 1 |
| M3 Nuts | 18 |
| M3 Inserts | 2 |

#### 3D Preparation

1. Clean the **Flying - 3D Kit** components thoroughly.
2. Insert **M3 Nuts**, **M3 Inserts**, **Output Bearings**, and **Transmission Bearings** in their corresponding slots in the 3D kit components.

#### Assembly

1. Secure the motor within the flying case A using 4 screws.
2. Position the 150mm timing belt around the motor's axle.
3. Install the encoder adjacent to the motor, and secure with nylon screws.
4. Place the ODRI 3D component, aligned with the 201mm timing belt. Close using flying case B and 6x20mm screws.
5. Attach the ODRI link and the extremity, securing with 15mm screws.

| [Top of page](#borinot-flying-arm-assembly-guide) | [Back to Hardware Building Instructions](README.md) | [Back to Borinot HOME](../README.md) | [Next → Lower Body Integration](7_lower_body_integration.md) |
| --- | --- | --- | --- |

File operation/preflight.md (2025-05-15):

# Procedure to fly :helicopter:

- To operate with **real robots** [go here](#11-pre-flight-checklist)
- To run a **simulation** [go here](#2-simulation).

## 1 Robot procedure
### 1.1 Pre-flight checklist

- [ ] 1. Place vehicle on the ground
- [ ] 2. Ensure the security net is well mounted
- [ ] 3. Turn the transmitter on
- [ ] 4. Enable the "kill switch"
- [ ] 5. Ensure that motors' screws are tight
- [ ] 6. Ensure that propellers tight
- [ ] 7. Ensure that propellers directions are correct
- [ ] 8. Connect the power battery
- [ ] 9. Leave the flight area
- [ ] 10. Place yourself behind the operator desk with the shield
- [ ] 11. Test kill switch: Arm motors and activate kill switch. The motors must stop.
- [ ] 12. Launch QGroundControl in the GCS
- [ ] 13. Switch to manual flight mode
- [ ] 14. Launch Optitrack node to add external estimation (see [here](#px4-optitrack-position-fusion))
- [ ] 15. Change to `posctl` flight mode
- [ ] 16. Check in QGroundControl that `posctl` is enabled

After this checklist you can proceed to fly manually or to launch other systems to allow autonomous operation.

### 1.2 PX4 Optitrack position fusion
We use an Optitrack system to provide good positioning ("fake GPS") to the PX4 system. 

The Optitrack positioning is streamed via UDP. This info is gathered by a ROS node (`vrpn_client`), which broadcast this into a ROS topic. A `mavros` node is then responible to subscribe to this topic, and send this information using a serial UART port and the MAVLink protocol to the Pixhawk. Finally, this position is fused inside PX4-EKF2 with the IMU and the other enabled sensors.

*TODO: Instructions on how to launch all required elements*

### 1.3 Connect PX4 with ROS2
>⚠️  **NOTE:** A prerequisite for this to work is that both (PX4 and `px4_ros_com`) have been built with the same set of messages. [See here for more info](build.md#121-urtps-bridge-configuration)
#### 1.3.1 Pixhawk 5x side
From the onboard computer do (you can connect it via SSH):
1. Access the MAVLink console `./Tools/mavlink_shell.py /dev/ttyACM0`. [More info here](https://docs.px4.io/master/en/debug/mavlink_shell.html)
3. In the MAVLink console, start the microRTPS client to start transmitting over ethernet: `micrortps_client start -t UDP -i 192.168.0.4`. Notice that the IP corresponds to the computer we want to connect with, which is the onboard computer (check the onboard computer's IP using `ifconfig`).

#### 1.3.2 Onboard computer side

1. Be sure to have configured the network setting with the correct IP (the same that you have used in the Pixhawk side).
2. Start the microRTPS agent. In a terminal from the onboard computer do: `./<path-to-ros2-ws>/install/px4_ros_com/bin/micrortps_agent -t UDP -i 192.168.0.3`.  The IP is the Pixhawk's IP.
3. Check in a separate terminal that the data is being received, e.g. `ros2 topic echo /fmu/vehicle_angular_velocity/out`

## 2 Simulation procedure
Simulation based on the SITL provided by PX4. This should be changed by our own simulation environment.

### 2.1 Simulation launch
Run the following command:
```console
foo@bar:~/$ cd <path-to-px4-autopilot>
foo@bar:<path-to-px4-autopilot>/$ make px4_sitl_rtps gazebo
```
### 2.2 Connect PX4 with ROS2
>⚠️  **NOTE:** A prerequisite for this to work is that both (PX4 and `px4_ros_com`) have been built with the same set of messages. [See here for more info](build.md#121-urtps-bridge-configuration)
#### 2.2.1 Pixhawk 5x side

The MicroRTPS Client inside the PX4 should be launched automatically. You can check its status typing the following command in the PX4 shell:
```
px4> micrortps_client status
```
If it is not running, you can start it with:
```
px4> mcirortps_client start -t UDP
```
#### 2.2.2 Onboard computer side
Start the microRTPS agent. In a terminal run the following command:

```console
foo@bar:~/$./<path-to-ros2-ws>/install/px4_ros_com/bin/micrortps_agent -t UDP
```

## 3 Other useful information

### 3.1 Launch a control node

 - For the control node available [see here](../eagle_mpc_2_control/README.md)

### 3.2 ROS2 bag
To record the data in ROS2:
```
ros2 bag record -a
```
### 3.3 Launching with FastDDS

[Explanation here](https://fast-dds.docs.eprosima.com/en/v2.3.3/fastdds/ros2/ros2.html)

Steps:

1. Export environment variable: `export RMW_IMPLEMENTATION=rmw_fastrtps_cpp`

2. When running a node: `RMW_IMPLEMENTATION=rmw_fastrtps_cpp ros2 run <package> <application>`

[Back to Procedures](README.md)

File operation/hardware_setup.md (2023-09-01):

# Hardware

This page should be moved once we have opened the UAM design. A repo to talk only about hardware should be opened. This piece of documentation belongs there.

# Connect Pixhawk 5x with ROS2

## Preparation

1. Connect the Pixhawk 5x ethernet cable to the computer port you want to communicate with
2. Connect the Pixhawk USB to a computer so that you can access the MAVLink console
3. Configure the wire network IP, e.g. `192.168.0.4`.

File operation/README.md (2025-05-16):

# Operation Guide

This page provides instructions for operating the Borinot using the nodes installed in it.

**Contents:**

0. [**Environment Setup**](1_environment_setup.md) - Flying area, Optitrack, Pre-flight checks.  
1. [**Borinot Bringup**](2_borinot_bringup.md) - Hardware checks, Radio controller, Software start up.
2. [**Laptop Bringup**](3_laptop_bringup.md) - Launch GUIs.  
3. [**Flight Procedure**](4_flight_procedure.md) - Protocol explaining how a standard flight is performed and which signs that should be looked for.

---
| [Top of page](#operation-guide) | [back to Borinot HOME](../README.md) |
| --- | --- |

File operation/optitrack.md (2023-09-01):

# Optitrack

[Back to Procedures](../README.md)

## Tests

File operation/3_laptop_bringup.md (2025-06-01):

# Laptop Bringup

## Launch borinot Graphical User Interface

``` bash
rosgalactic_cyclone
ros2 launch eagle_ros2_viz bringup_gui.launch.py robot_name:=borinot_flying_arm_2
```

Two GUI windows are opened:
- [Borinot's State:](#borinot-state) Visualizer for Borinot internal state (pose, orientation, etc)
- [MPC Interface:](#mpc-interface) Control the mpc and the arm
> ⚠️⚠️ The MPC Interface is used to send commands: be careful about the values you are sending!! ⚠️⚠️

The two GUIs are explained below.

**Tip:** Don't close these windows between flight as you can load previous command through the History

### Borinot state

In **Borinot state** you can read the state of Borinot:

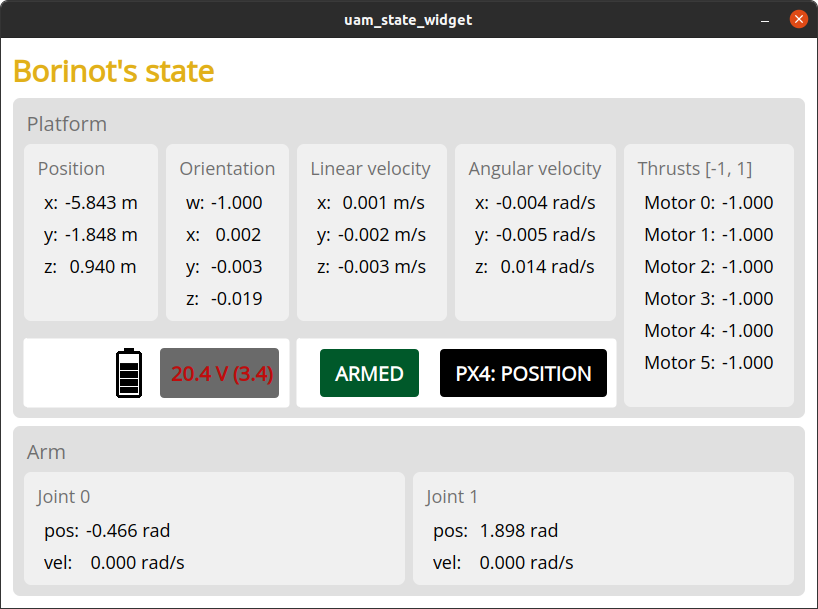
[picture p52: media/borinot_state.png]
Borinot State
  

### MPC Interface

In **MPC Interface** you control the robot using MPC.

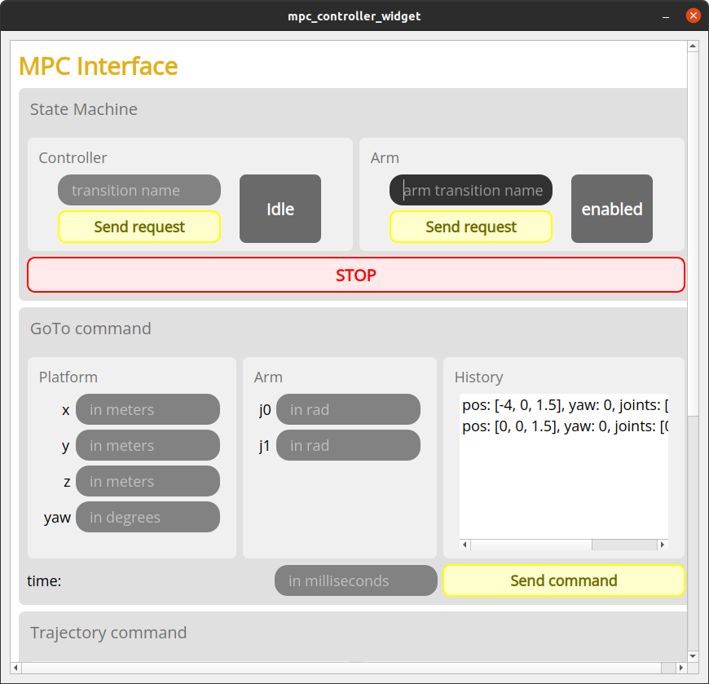
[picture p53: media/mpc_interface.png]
MPC Interface
  

This GUI contains three sections:

1. **State Machine:** controls and displays the state machines of Borinot. There's the Controller state machine and the Arm state machine.

   In the controller state machine, states and state transition commands are as follows:

   ```
              enable                 
   +------+   ------>   +---------+   start   +---------+
   | Idle |             | Enabled |  ------>  | Running |
   +------+   <------   +---------+           +---------+
       ∧      disable                              |
       |___________________________________________|
                          disable
   ```

   In the arm state machine, states and state transition commands are as follows:

   ```
              enable                 
   +------+   ------>   +---------+   start   +---------+
   | Idle |             | Enabled |  ------>  | Running |
   +------+   <------   +---------+           +---------+
       ∧      disable                              |
       |___________________________________________|
                      stop / disable
   ```

   The button `STOP` will stop both state machines at once. The arm is disabled and the platform switches to POSITION CONTROL MODE.

   To send commands, write the commands `enable`, `start` or `disable` in the 'transition name' window and press ENTER or click on 'send command'. The gray window on the right will display the new state.

2. **GoTo command**

   This section allows you to send waypoints to the controller. Follow these steps:
   - Enter desired XYZ and Yaw for the pose of the base, and j0, j1 for the arm angles.
   - Enter the travel time in milliseconds
   - Press ENTER or click 'Send command'

3. **Trajectory command**

   This section allows you to select a trajectory to execute. (⚠️ TODO revise)
   - Enter the trajectory name
   - Enter the controller type (use only RAIL MPC)
   - Enter the controller
   - Press ENTER or click 'send command' 

<!-- ## Additional procedures and troubleshooting

In addition to the preflight safety checklist, this page also contains documentation for other procedures that are necessary for operating the Borinot UAM. These include:

### [Troubleshooting](troubleshooting.md)

The [troubleshooting.md](troubleshooting.md) file contains a list of known issues and troubleshooting tips to help you quickly resolve problems that may arise during UAM operation.

If you encounter any difficulties during assembly or setup, our [Troubleshooting](resource/troubleshooting.md) section is here to help.

## How to Use Borinot
To use Borinot, we've made a set of guides to help you get started with it:

- [Preflight Checks](resource/preflight.md) - This document contains a checklist of preflight checks that must be performed before operating Borinot to ensure its safety and reliability.
- [Optitrack fusion](resource/optitrack.md) - This document explains how to fuse data from the Optitrack motion capture system and the PX4 flight controller to obtain accurate position and orientation estimates for Borinot.
- [MPC Controller](resource/mpc.md) - This document provides an overview of the Model Predictive Controller (MPC) used to control Borinot's hybrid locomotion, and explains how to run simulations and experiments with the controller. -->

---
| [Top of page](#laptop-bringup) | [Back to Operations](./README.md) | [back to Borinot HOME](../README.md) | [Next → Flight Procedure](4_flight_procedure.md) |
| --- | --- | --- | --- |

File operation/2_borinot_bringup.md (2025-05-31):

# Borinot Bringup

## Part 1: Hardware Checks
1. Check the motors:
   - [ ] Try to rotate the motor case, if it is loose, it the inside screws should be tightened
   - [ ] If some motor cables have been disconnected, check the motor ID and the spin direction. Spin direction must follow this convention: [Hexarotor X airframe reference](https://docs.px4.io/main/en/airframes/airframe_reference.html#hexarotor-x)
   - [ ] Check unusual noise in pitch. If present, the motor should be cleaned for attached metal on the magnets
2. Check upper body:
   - [ ] Wifi antenna should be in its upright position (pointing up)
3. Check lower body:
   - [ ] Check connectors (Ethernet, microdriver + masterboard) are connected
   - [ ] The arm should be streched (pointing down)

## Install the propellers
1. Check that the propellers are not damaged
2. Use the following color convention: red for front, blue for the rest
3. Check that they respect the orientation of the [Hexarotor X airframe reference](https://docs.px4.io/main/en/airframes/airframe_reference.html#hexarotor-x)
4. Tighten the propeller

 When everything tight, turn on Borinot (with the power supply at 22.5V)

## Prepare radio controller
- Put batteries in it (4x AA Batteries)
- Check if the radio controller detects the receiver (`RX` battery bar should have a voltage level -> should not be `?`)
> ⚠️  If the radio controller does not detect the receiver, the receiver need to be bind to the radio controller
>  - on the receiver, connect a jumper to the bypass pins
>  - on the radio controller, start binding procedure (setting icon,`RX bind`)
- Activate the Kill Switch (red switch in down position)

## Part 2: Software Start Up

> ⚠️ **User at laptop** Login at the HiDRo laptop with user "hidro_admin".

Inside Borinot `ssh borinot-X`, usually `X=1`:
1. Start `micrortps_client` in pixhawk:
    ``` bash
    ssh borinot-X
    rosgalactic_cyclone
    ./start_px4.sh
    # copy/paste the command inside the Mavlink Shell
    # the command looks like this:
    #    micrortps_client start -t UDP -i 192.168.0.4
    ```
   -A micrortps command will be printed in the Mavlink Shell (terminal).
   - copy/paste the command inside the Mavlink Shell
   - the command looks like this, but copy/paste that on the terminal:
      -  `micrortps_client start -t UDP -i 192.168.0.4`
  
2. Start ros2 launch file for the system:
    ``` bash
    ssh borinot-X
    rosgalactic_cyclone
    ros2 launch eagle_ros2_bringup borinot_flying_arm_2_system.launch.py
    # the password will be asked if the arm does not start
    # sometimes it is not asked: type the password anyway
    ```
    - You should see that the `vrpn _client_node` has found `borinot_fur_ot`, if not, got to troubleshooting
    - You should see `Connection established`
    - After that, enter the password (not explicitly demanded) and click enter
    - You should see `Using Ethernet (xxxxxxx)`
    - These two instructions I dont understand:
       - If `robot_interface` does not start (TODO: then what?)
       - `Warning` message should not be consider has an error (TODO: what?)
3. When using the MPC, launch the MPC:
    ``` bash
    ssh borinot-X
    rosgalactic_cyclone
    ros2 launch eagle_ros2_bringup borinot_flying_arm_2_mpc.launch.py
    ```
4. If you need to record data, record inside Borinot
    ``` bash
    ssh borinot-X
    rosgalactic_cyclone
    ros2 bag record -a
    ```

---
| [Top of page](#borinot-bringup) | [Back to Operations](./README.md) | [back to Borinot HOME](../README.md) | [Next → Laptop Bringup](3_laptop_bringup.md) |
| --- | --- | --- | --- |

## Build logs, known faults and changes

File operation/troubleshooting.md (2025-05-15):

# Troubleshooting
## Problem 1:
### Error:

`what():  Unexpected byte value in Cdr::deserialize(bool), expected 0 or 1`

### Diagnostic:

PX4 messages are different from the ROS2 messages

### Solution:

1. Generate ROS2 messages using the python script
2. Remove build/ install/ log/ folders from ROS2 workspace (only px4_msgs folders)
3. Compile again ROS2 workspace

[Back to Procedures](../README.md)

## Problem: motor not spinning at the same speed

### Recalibrate the esc

## ERROR at motor driver ## : SPI Receiver timeout
- This error can occur randomly
- to solve it:
  1. kill `system.launch.py` 
  2. restrech the arm (pointing down)
  3. disconnect and reconnect the two power cables (udriver and master board)
  4. restart the `system.launch.py`
  5. reable the arm throught the MPC Interface
  6. If the arm is in it's correct starting position, you are good!

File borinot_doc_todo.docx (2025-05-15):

### Repo Doc: https://github.com/Bacmel/Borinot

### images folder (https://drive.google.com/drive/folders/1sKhCaoJuHLcfh3QGO7MWCxbDfbXwcxNZ?usp=drive_link)

### General

- Add all the tricky and important things that you can think
- insert_nut.jpg to give a tip on how to insert it.

### Component list (https://github.com/Bacmel/Borinot/blob/main/hardware/0_components_list.md)

- Component list -> Add images of all the components to visual check that you have all you need to build a new one. Divide in sections (upper_body, motor case, limb&legs and landing) with a picture of all components in each section with names.
- Component list -> add a column to know where is stored
- Check the links, but maybe, if we have the visual information already in pictures, it’s not necessary any link. We have the reference and at the time to buy qe con google each reference. Just saying it because it seems difficult to keep the links working. If you think that is important the link to know where to buy it, maybe just the link of the home page is okey in a shopping colum or whatever.
- ø**...**mm O-ring Seals ????
- I don’t understand the difference between the component list and the bill of materials
- 3D printed parts don’t say anything to me without a visual reference.
- 3d printed -> motor case -> cache is cover??
- Add a link to next page at the end.

### How to print.

- Add a page with the necessary information of how to print the different parts. Where to find the cat files, any configuration necessary to be well printed, the color if it’s necessary a specific color, if it is necessary a specific 3d printer… I don’t know, whatever it may be important

### Component preparation guide (https://github.com/Bacmel/Borinot/blob/main/hardware/1_component_preparation.md)

Part 1

- Add boxes with #id and add a column to the component list with an #id to match the components with the visual info. That id can be added in the instruction to easily check the components.
- reference (links) not working. Same as last point. If there is a visual information with pictures, maybe just with the reference and website where to buy it, is enough.
- Add a column to know where they are. Maybe it is enough with workshop (WS), Hidro shelves (HS) and to print (P). Maybe inside HS is important to know where (blue box, white box… I don’t know)
- ~~https://github.com/hidro-iri/Borinot/blob/main/hardware/brushless_motor_esc.md#part-2-esc-modification~~ ~~-> How I know where are the signal pads?~~
- ~~Add at the end of each “chapter” the link to the next one.~~
- Add all the things that you found tricky in the process.
- For alopez. If I have the opportunity, change the image without heat shrink to a lateral one to see all the connections.
- Just silly, add a separator between the last instructions and the image of the following instructions. I think the picture is related to the last instruction.
- Add image microdriver_cable_finished.jpg (between 8 and 9)
- step 14 warning i think it goes in step 13
- step 15 -> add the heat shrink to cover the pins and maybe change the red cable to the other cable because in that case it is green.
- step 18 -> add heat shrink to cover the pins.

Part 2

- Same for component table
- step 2 -> If you think is important that the cables are soldered in the middle, not touching the banana connector border, just say it
- ESC modification -> missing back image. For me, add a box to the things to show.
- Well, I don’t know what you think, but I have modified all the cables adding the connectors and at the end soldered them to the ESC. If crimping a single cable is a pain in the ass, if it is also soldered to an esc with another 6 cables soldered…. It can be a good way to torture someone XD
- step 12 -> Double-check the orientation.?? which orientation?? Add esc_servo_crimp.jpg image??

### Air frame assembly guide (https://github.com/Bacmel/Borinot/blob/main/hardware/2_airframe_assembly.md)

Part 1:

- Add airframe_components.jpg with labeled components
- Change the first image with motor_case_parts.jpg labeling the name of each part
- M4x10mm Nylon not true. Explain the process (cut one bigger)
- step 2 -> add also according to the following table.
- step 2 -> Add explanation that orange ones are in the front.
- step 2 -> Clarify what is test-fit. add middle_diference.jpg picture to show it. Add that it must match with the upper and lower part (and, between them at the end)
- I prefer start image and end image at the same level.
- (optional) add opt_markers.jpg to check that is correct
- step 4 -> How do you assemble it? Which glue is necessary?

Part 2:

- Specify the head of the screw and in the large one if is necessary to be all screwed or not (just cilindric after the head or not)
- we don’t have M3x05mm Screws, just 06mm.
- Change the pictures for the new ones matching the haxarotor-x reference.
- step 1 -> Remove o rings information and maybe that step. I’m not assembling anything
- step 2 -> move the table to here. Add left_right_motor.jpg image to explain the sides.
- Remove all heat shrink reference
- So, after doing it. I will put in the first step before, the explanation to assemble one triangle and two motors of the other triangle and after that we will merge both triangles and after, assemble the last motor (step 4,5 and 6). Step 1 is the step 3. Suggestion -> Step 2: attach tubes. Select a motor. Insert the 4 30mm screws. Put something to keep the screws in its position (ball of paper) as shown in picture attach_tubes.jpg. Insert the rest of the motor parts taking into account when it is necessary to insert between parts a fiber tube. Add the motor at the top. Turn it around pressing the motors to keep all the “sandwich” intact. Remove the paper ball. screw it keeping the pressure in the motor.
- ~~I think that step 3 must be before step 2~~
- ~~I think step 4, 5 and 6 are the explanation of the order of the assembly. I think it must be before, not the final steps~~
- step 2 -> Add the explanation that the nuts of the screws are the motors. Add the explanation of the position of each motor (not covering the marker)
- Add at the end airframe_finished.jpg

Part 3

- Install ecs: Insert first the power side of the esc and after the motor phases one. Add esc_installed.jpg
- Put picture for esc signal and power cables routing
- Connect the motor phases to their closer ones.

### Upper body (https://github.com/Bacmel/Borinot/blob/main/hardware/3_main_body_assembly.md)

part 1

- Add upper_body_comp.jpg with labels. If a 3d parts it’s called in any way in the instructions, label it also. Add also pixhawk.jpg and radio_receiver.jpg (missing radio receiver cable)
- specify head of screws.
- Pay special attention to the marker holders and fastener holders. marker holders?? fastener holders??
- Change dots to steps.
- How to create the dumpers (earplug_tool.jpg)
- How to fix the dumpers? (Glue)
- First put m3 nuts, after dumpers in the pixhawk case.
- Explain the trick to put the nuts in the pixhawk case.
- A suggestion on how to put nuts in holes (screwdriver and hammer in my case)
- the pixhawk fastener must have the head outside (pixhawk_fateners.jpg)
- How to cut Square carbon fiber tubes (dremel??)
- How to fix carbon fiber tubes? (fasteners instructions)

part 2

- Attach the Wi-Fi antenna to the Pixhawk case using fasteners. -> disconnect the antenna
- Missing step to insert carbon fiber tubes before power module
- add instructions of where cables must be inserted and the order if important
- add power_module_assembled.jpg
- Before screwing the power module, insert blue connector and diode connector. (maybe not necessary with new design)
- Secure the Ethernet adapter and radio receiver to the top part using fasteners (do not tight the radio receiver - it should be tightened during the cable routing for an easyer routing). radio receiver???? secure also the usb connector of the ethernet adapter (NO)?? eth_radio_assembled.jpg. Add explanation on how to connect radio receiver cable.
- Remove all connect things and put it at the end?
- pixhawk connections -> power1 and eth. before eth to pixhawk pass it through the hole. power at the side of the antenna. add pixhawk_box_assembled.jpg
- Position the bottom part of the main body inside the contour part. -> in the pictures is not. Do we have to do it at that point?
- Insert the 150mm square carbon fiber tubes into the top and bottom parts of the main body case. -> just the bottom, the upper must be inserted before
- Think like 1. prepare single element (top, contour, bottom :warning: positionate the cables properly before 2), 2.¨ ässemble¨, 3. connect he cable
- nuc: usually, 1. connect the power supply, 2. install bottom inside contour Position????, 3. install nuc in the main body
- For Patrick: on the contour part, the material ove the power cable of the nuc should be remove to facilitate the installation.
- Add mainbody_orientation.jpg image
- Insert the 150mm square carbon fiber tubes into the top and bottom parts of the main body case. -> Add pushing them until the end.
- Add fastened lower part before screwing the nuc.
- add upper_and_lower assembled.jpg (and use it to specify the front)
- Add instructions to insert the nuts of main body markers (M4). Decide if for the upper boy we use nuts or insertions and add the instructions of the insertions before assembling the nuc.

### Upper body integration (https://github.com/Bacmel/Borinot/blob/main/hardware/4_upper_body_integration.md)

- Add images: cable_prev.jpg,cable_prev2.jpg (choose one), usbc_cable.jpg (components), big_spacer.jpg, airframe_mainbody_orientation.jpg, 3d_integration_comp.jpg (missing smaller ones for small spacers), integration_comp.jpg, medium_spacer.jpg. small_spacer.jpg
- For the routing modify cable_prev.jpg or cable_prev2.jpg
- Missing pictures of the routing
- first pixhaw power
- first pass through the hole the motor signals, after connect the power cables of motors and after that connect all of them. Connect the receiver cable
- After route usbC and eth from pixhawk
- add images: route_radio_esc.jpg, route_pixhawk_power.jpg, route_ethernet_antenna.jpg, route_radio_antennas.jpg, route_usbs_c_eth.jpg, route_down_cables.jpg and route_finished.jpg

### Landing gear assembly (https://github.com/Bacmel/Borinot/blob/main/hardware/5_landing_gear_assembly.md)

- Image with all components (landing_comp.jpg) missing components to fix the “wheels” to the carbon tube and the instructions.
- Specify screw heads
- How to cut carbon fiber tubes
- change dots by steps
- add land_base.jpg
- Join the cross-block connectors using the 170mm carbon fiber tubes, ensuring alignment with provided images. Create two such assemblies. -> 4x 110mm
- tip, force into the tube while moving the angle until match with the right orientation.
- add land_vertical.jpg
- Assemble the entire landing gear by integrating the previously made assemblies with the 4 110mm carbon fiber tubes. Follow the reference images for accurate alignment. -> 2x 170mm
- add land_legs.jpg and land_gear.jpg
- Add instructions to assembly “wheels” to the landing gear. Add 4 inserts and 20mmm M3 cone head screws.
- When do we have to screw to fix each bar. How much to not broke the 3d parts.
- For the “feet” 16mm screw
- add land_gear_finished.jpg

### Check motor ids and directions and that don’t need to be cleaned.

Add instructions to how to clean it.

Maybe flash before the pixhawk

before check with hand that spin well

Connect borinot to a power supply (hot swap) cable and to the hidro computer (usbC). Text with QGroundControl. -> ready to flight -> vehicle setup -> motors

with airframe X we will check if the motors are in the correct id(1-6). Check also the direction with a paper

### Pixhawk installation (https://github.com/Bacmel/Borinot/blob/main/software/1_pixhawk_configuration.md#1-installation)

I have just follow that instructions

In NUC:

mkdir libraries && cd libraries

git clone --branch v1.3.1 https://github.com/eProsima/foonathan_memory_vendor.git

cd foonathan_memory_vendor && mkdir build && cd build

cmake -DCMAKE_BUILD_TYPE=Release ..

make -j6

sudo make install

cd ~/libraries

git clone –branch v2.0.2 https://github.com/eProsima/Fast-DDS.git

cd Fast-DDS

git submodule update --init --recursive

mkdir build && cd build

cmake -DTHIRDPARTY=ON -DSECURITY=ON ..

make -j6

sudo make install

cd ~/libraries

git clone --branch v1.0.4 –recursive https://github.com/eProsima/Fast-DDS-Gen.git

cd Fast-DDS-Gen

git submodule update --init --recursive

cd gradle/wrapper/

vim gradle-wrapper.properties change DistributionUrl to 6.8.3

cd ../..

./gradlew assemble && sudo env "PATH=$PATH" ./gradlew install

pip install empy==3.3.4

Saltamos a este punto

cd ~/libraries/PX4-Autopilot/

make px4_fmu-v5x_rtps upload

—--------

### Eagle (https://github.com/Bacmel/Borinot/blob/main/software/2_eagle_mpc_installation.md)

- ~~2 -> modify .bashrc -> add before a line to know that is for crocoddyl (# Crocoddyl)~~
- ~~3 -> change for sudo apt install -qqy robotpkg-py38-eigenpy=2.8.0 robotpkg-hpp-fcl=1.8.1 robotpkg-py38-hpp-fcl=1.8.1 robotpkg-pinocchio=2.6.10 robotpkg-py38-pinocchio=2.6.10 robotpkg-py38-example-robot-data~~
- ~~sudo apt install -qqy robotpkg-py38-eigenpy=2.8.0 \~~
- ~~robotpkg-py38-example-robot-data \~~
- ~~robotpkg-hpp-fcl=1.8.1 \~~
- ~~robotpkg-py38-hpp-fcl=1.8.1 \~~
- ~~robotpkg-pinocchio=2.6.10 \ robotpkg-py38-pinocchio=2.6.10~~
- git clone https://github.com/hidro-iri/eagle_mpc_lib.git -b bfa2_experiments -> or public or change to git clone git@github.com:hidro-iri/eagle_mpc_lib.git -b bfa2_experiments
- solve eagle_mpc example problem or delete it in doc

### Master board (https://github.com/Bacmel/Borinot/blob/main/software/3_master_board_configuration.md)

- Part 2: Odri Control Interface Installation
- Add explanation of the examples and what we are expecting. Stop it with ctrl+C.

### ROS2 (https://github.com/Bacmel/Borinot/blob/main/software/3_ros2_install_config.md)

- sudo apt update
- sudo apt install python3-vcstool
- mkdir ~/galactic_ws && cd ~/galactic_ws
- wget https://raw.githubusercontent.com/Bacmel/Borinot/refs/heads/main/resource/borinot.repos

### leg microcontroller installation

### hidro laptop

### Troubleshooting (https://github.com/Bacmel/Borinot/blob/main/resource/troubleshooting.md)

- Check battery level before flight (23,5V)

## To Print

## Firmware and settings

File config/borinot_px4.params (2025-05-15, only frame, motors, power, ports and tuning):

1	1	BAT1_CAPACITY	-1.000000000000000000	9
1	1	BAT1_N_CELLS	6	6
1	1	BAT1_R_INTERNAL	-1.000000000000000000	9
1	1	BAT1_SOURCE	0	6
1	1	BAT1_V_CHARGED	4.199999809265136719	9
1	1	BAT1_V_EMPTY	3.500000000000000000	9
1	1	BAT1_V_LOAD_DROP	0.300000011920928955	9
1	1	BAT2_CAPACITY	-1.000000000000000000	9
1	1	BAT2_N_CELLS	0	6
1	1	BAT2_R_INTERNAL	-1.000000000000000000	9
1	1	BAT2_SOURCE	-1	6
1	1	BAT2_V_CHARGED	4.050000190734863281	9
1	1	BAT2_V_EMPTY	3.500000000000000000	9
1	1	BAT2_V_LOAD_DROP	0.300000011920928955	9
1	1	BAT_CRIT_THR	0.070000000298023224	9
1	1	BAT_EMERGEN_THR	0.050000000745058060	9
1	1	BAT_LOW_THR	0.150000005960464478	9
1	1	BAT_N_CELLS	5	6
1	1	BAT_V_CHARGED	4.050000190734863281	9
1	1	BAT_V_EMPTY	3.500000000000000000	9
1	1	BAT_V_LOAD_DROP	0.300000011920928955	9
1	1	MC_PITCHRATE_D	0.003000000026077032	9
1	1	MC_PITCHRATE_FF	0.000000000000000000	9
1	1	MC_PITCHRATE_I	0.000000000000000000	9
1	1	MC_PITCHRATE_K	2.000000000000000000	9
1	1	MC_PITCHRATE_MAX	220.000000000000000000	9
1	1	MC_PITCHRATE_P	0.150000005960464478	9
1	1	MC_PITCH_P	6.500000000000000000	9
1	1	MC_ROLLRATE_D	0.003000000026077032	9
1	1	MC_ROLLRATE_FF	0.000000000000000000	9
1	1	MC_ROLLRATE_I	0.000000000000000000	9
1	1	MC_ROLLRATE_K	2.000000000000000000	9
1	1	MC_ROLLRATE_MAX	220.000000000000000000	9
1	1	MC_ROLLRATE_P	0.150000005960464478	9
1	1	MC_ROLL_P	6.500000000000000000	9
1	1	MC_YAWRATE_D	0.000000000000000000	9
1	1	MC_YAWRATE_FF	0.000000000000000000	9
1	1	MC_YAWRATE_I	0.000000000000000000	9
1	1	MC_YAWRATE_K	2.000000000000000000	9
1	1	MC_YAWRATE_MAX	200.000000000000000000	9
1	1	MC_YAWRATE_P	0.200000002980232239	9
1	1	MC_YAW_P	2.799999952316284180	9
1	1	MC_YAW_WEIGHT	0.400000005960464478	9
1	1	MOT_ORDERING	0	6
1	1	MOT_SLEW_MAX	0.000000000000000000	9
1	1	PWM_MAIN_DIS1	900	6
1	1	PWM_MAIN_DIS2	900	6
1	1	PWM_MAIN_DIS3	900	6
1	1	PWM_MAIN_DIS4	900	6
1	1	PWM_MAIN_DIS5	900	6
1	1	PWM_MAIN_DIS6	900	6
1	1	PWM_MAIN_DIS7	900	6
1	1	PWM_MAIN_DIS8	900	6
1	1	PWM_MAIN_FAIL1	-1	6
1	1	PWM_MAIN_FAIL2	-1	6
1	1	PWM_MAIN_FAIL3	-1	6
1	1	PWM_MAIN_FAIL4	-1	6
1	1	PWM_MAIN_FAIL5	-1	6
1	1	PWM_MAIN_FAIL6	-1	6
1	1	PWM_MAIN_FAIL7	-1	6
1	1	PWM_MAIN_FAIL8	-1	6
1	1	PWM_MAIN_MAX1	2000	6
1	1	PWM_MAIN_MAX2	2000	6
1	1	PWM_MAIN_MAX3	2000	6
1	1	PWM_MAIN_MAX4	2000	6
1	1	PWM_MAIN_MAX5	2000	6
1	1	PWM_MAIN_MAX6	2000	6
1	1	PWM_MAIN_MAX7	2000	6
1	1	PWM_MAIN_MAX8	2000	6
1	1	PWM_MAIN_MIN1	1000	6
1	1	PWM_MAIN_MIN2	1000	6
1	1	PWM_MAIN_MIN3	1000	6
1	1	PWM_MAIN_MIN4	1000	6
1	1	PWM_MAIN_MIN5	1000	6
1	1	PWM_MAIN_MIN6	1000	6
1	1	PWM_MAIN_MIN7	1000	6
1	1	PWM_MAIN_MIN8	1000	6
1	1	PWM_MAIN_REV1	0	6
1	1	PWM_MAIN_REV2	0	6
1	1	PWM_MAIN_REV3	0	6
1	1	PWM_MAIN_REV4	0	6
1	1	PWM_MAIN_REV5	0	6
1	1	PWM_MAIN_REV6	0	6
1	1	PWM_MAIN_REV7	0	6
1	1	PWM_MAIN_REV8	0	6
1	1	PWM_MAIN_TRIM1	0.000000000000000000	9
1	1	PWM_MAIN_TRIM2	0.000000000000000000	9
1	1	PWM_MAIN_TRIM3	0.000000000000000000	9
1	1	PWM_MAIN_TRIM4	0.000000000000000000	9
1	1	PWM_MAIN_TRIM5	0.000000000000000000	9
1	1	PWM_MAIN_TRIM6	0.000000000000000000	9
1	1	PWM_MAIN_TRIM7	0.000000000000000000	9
1	1	PWM_MAIN_TRIM8	0.000000000000000000	9
1	1	SYS_AUTOSTART	6001	6

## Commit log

2023-09-01 feat: :rocket: Move borinot repo
    [cache_cable.STEP, case_controller_bottom.STEP, case_controller_top.STEP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]
2025-03-04 refactor: :art: Format the structure for the assembly documentation
2025-03-05 fix: :memo: Add more info for power module
2025-03-05 feat: :memo: Refactor airframe assembly doc
2025-03-19 feat: :memo: Init master board configuration file
2025-03-19 refactor: :memo: Init final assembly file
2025-03-20 Add px4 parameters
    [borinot_px4.params]
2025-03-21 refactor: :memo: Add operation folder
    [borinot_px4.params]
2025-04-04 refactor: :memo: Push current hardware documentation
    [borinot_px4.params]
2025-04-07 Add current state of the doc
    [cache_cable.STEP, case_controller_bottom.STEP, case_controller_top.STEP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]
2025-05-15 Document optitrack IMU center setup
